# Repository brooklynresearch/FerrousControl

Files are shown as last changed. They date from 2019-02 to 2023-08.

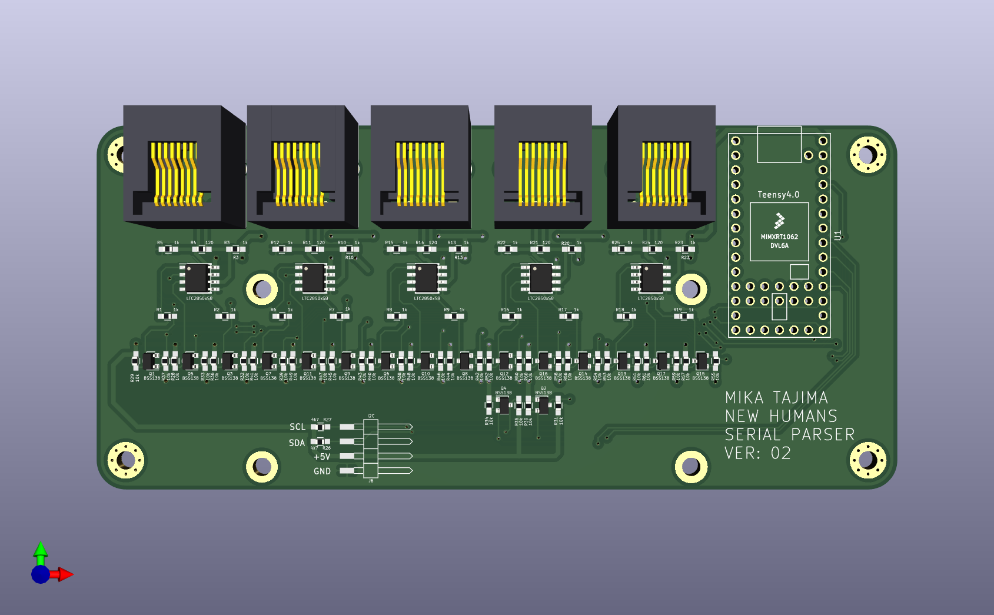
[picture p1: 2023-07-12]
embedded/hardware/SerialParser_V2/SerialParser_V2_Top.png

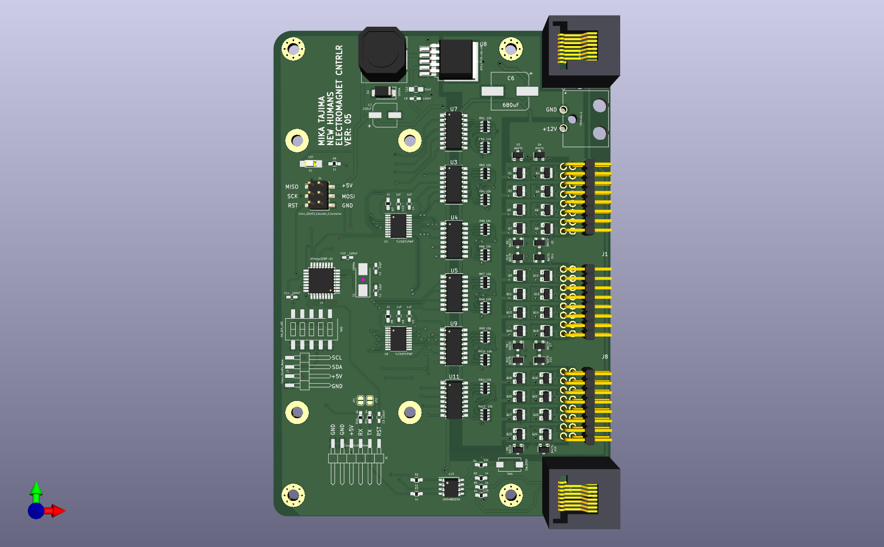
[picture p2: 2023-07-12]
embedded/hardware/ElectromagnetController_V5/ElectromagnetController_V5_top_view.png

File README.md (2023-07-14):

# FerrousControl
Ferrofluid controlled through an electromagnetic array

## python
This folder contains all the algorithms and code to send to the electromagnetic array.

## embedded
This folder contains all the design files and embedded code for the electromagentic controller boards.
These basically received USB Serial messages from the main computer, parse that information to the proper board, and translate those messages to the electromagnets.

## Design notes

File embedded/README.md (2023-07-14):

# Embedded

## hardware
This folder contains the schematics and board layout files for the electromagnetic controller and the serial parser boards.

## production
This folder contains all the production files for the electromagnetic controller and serial parser boards.

## software
This folder contatins all the arduino code and libraries used for both the electromagnetic controller and serial parser boards.

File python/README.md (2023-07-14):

# FerrousControl
Ferrofluid controlled through an electromagnetic array

## COMMS
Requirements:
- Python 3.6.2
- PySerial
- [Robust Serial Library](https://github.com/araffin/arduino-robust-serial)

## PYTHON
- steps variable in snake effectively changes speed with fewer steps being faster
- framerate also adjusts speed but for everything at once
- keyboard toggle for modes needs rewrite
- original code may have an issue with viscosity in fluid class with viscosity

## Startup
- java -jar /Users/newhumans/Documents/GitHub/FerrousControl/COMMS/PYTHON/nstokes_2_40x46/processing-py.jar /Users/newhumans/Documents/GitHub/FerrousControl/COMMS/PYTHON/nstokes_2_40x46/nstokes_2_40x46.pyde
- above was done as part of a Utilities Automator script that starts on login

### Resources
- [USB Serial Communication](https://www.pjrc.com/teensy/td_serial.html)
- [Serial Benchmark](https://www.pjrc.com/teensy/benchmark_usb_serial_receive.html)
- [TLC59711 Datasheet] (https://www.ti.com/lit/ds/symlink/tlc59711.pdf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)

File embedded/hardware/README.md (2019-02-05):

# FerrousControl
Ferrofluid controlled through an electromagnetic array

## PCB DESIGN
Using Eagle for CAD work.  Go to folder for more information

## RASPBERRY PI CODE
To be uploaded, with any steps for set up and functionality.

## EMBEDDED CODE
TO DO

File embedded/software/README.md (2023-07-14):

# Software
Arduino Based Code for both the Electromagnetic Controller and Serial Parser.

## Notes on the Electromagnetic Control
Code was based on the atmega328 chip set, however due to supply chain issues we used the atmega168 chip set.
Regardless, we needed to modify the hardware serial buffer to support 256 bytes, which was required in order to allow for full throughput of serial data.  The default serial buffer size is set to 64 bytes, and would cause overflow on the data being received on the RS485 line.
Liquid Crystal display is not needed, an only used for testing and feedback purposes.  It can be removed if needed.

## Notes on the Serial Parser
Code was based on the Teensy 4.0 development board.  
Liquid Cyrstal display is not needed, an only used for testing and feedback purposes.  It can be removed if needed.

## Platform
- Tested on Arduino 2.11

## Dependecies:
- [Teensyduino](https://www.pjrc.com/teensy/teensyduino.html)
- [MiniCore] (https://github.com/MCUdude/MiniCore)
- [LiquidCrystal_I2C] (https://github.com/johnrickman/LiquidCrystal_I2C)
- [TLC59711] (https://github.com/s-light/ulrichstern_Tlc59711/tree/master/examples)

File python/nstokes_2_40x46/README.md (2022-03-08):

# nstokes version 2
### 40 x 46 magnets

#### Launch Command
```
java -jar processing-py.jar nstokes_2_40x46.pyde
```

#### Keyboard Controls
* `s` Toggle SNEK mode
* `m` Toggle MORPH mode
* `t` Toggle test sequence (if snek or morph is active, toggle that off before using this)
* `o` All magnets on
* `r` Reset all to 0
* `f` Activate area around mouse pointer
* `d` Activate single magnet under mouse pointer

#### Notes

To change the parser board USB addresses, edit the [serialAddresses array](https://github.com/brooklynresearch/FerrousControl/blob/772c967f043f15182d9b4fa4592e4093779d1fde/COMMS/PYTHON/nstokes_2_40x46/nstokes_2_40x46.pyde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)

To have the program run the test sequence only, set [DEBUG_MODE](https://github.com/brooklynresearch/FerrousControl/blob/772c967f043f15182d9b4fa4592e4093779d1fde/COMMS/PYTHON/nstokes_2_40x46/nstokes_2_40x46.pyde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)

**Possible issue**: I've had to restart the parser boards to get the magnet indexing correct. This seems to happen when connecting a magnet controller (or chain of them) to one of the parser's RJ45 ports **after** running the processing sketch.
Sometimes, subsequent runs will have incorrect indexing for the packet that gets sent to the magnet boards. For example, the boards in the lower half will be one row off until a parser restart.
Replugging the USB hub to the computer fixes it. **Needs more testing**

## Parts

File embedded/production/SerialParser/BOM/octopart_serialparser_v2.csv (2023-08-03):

Query | Qty | Manufacturer | MPN | Octopart URL | Part Description | Description | Schematic Reference | Internal Part Number | Lifecycle | Lead Time | RoHS | Total Qty (@ Batch Size: 1) | SKU | SKU | SKU | SKU | SKU | Packaging | Packaging | Packaging | Packaging | Packaging | Unit Price (@ Batch Size: 1) | Unit Price (@ Batch Size: 1) | Unit Price (@ Batch Size: 1) | Unit Price (@ Batch Size: 1) | Unit Price (@ Batch Size: 1) | In Stock | In Stock | In Stock | In Stock | In Stock | MOQ | MOQ | MOQ | MOQ | MOQ | URL | URL | URL | URL | URL | Distributor [Lowest Price (Selected)] | SKU [Lowest Price (Selected)] | Packaging [Lowest Price (Selected)] | Unit Price (@ Batch Size: 1) [Lowest Price (Selected)] | Line Total [Lowest Price (Selected)] | Batch Total [Lowest Price (Selected)] | In Stock [Lowest Price (Selected)] | MOQ [Lowest Price (Selected)] | URL [Lowest Price (Selected)] | Notes
 |  |  |  |  |  |  |  |  |  |  |  |  | Digi-Key | Mouser | Newark | Onlinecomponents.com | RS Components | Digi-Key | Mouser | Newark | Onlinecomponents.com | RS Components | Digi-Key | Mouser | Newark | Onlinecomponents.com | RS Components | Digi-Key | Mouser | Newark | Onlinecomponents.com | RS Components | Digi-Key | Mouser | Newark | Onlinecomponents.com | RS Components | Digi-Key | Mouser | Newark | Onlinecomponents.com | RS Components
RNCP0603FTD10K0 | 34 | Stackpole Electronics | RNCP0603FTD10K0 | https://octopart.com/rncp0603ftd10k0-stackpole+electronics-19220255 | Res Thin Film 0603 10K Ohm 1% 1/8W ±100ppm/°C Molded SMD SMD Paper T/R |  | R28, R29, R30, R31, R32, R33, R34, R35, R36, R37, R38, R39, R40, R41, R42, R43, R44, R45, R46, R47, R48, R49, R50, R51, R52, R53, R54, R55, R56, R57, R58, R59, R60, R61 |  |  | 14w | Compliant | 34 | RNCP0603FTD10K0CT-ND | 708-RNCP0603FTD10K0 |  | RNCP0603FTD10K0 |  | Cut Tape | Tape & Reel |  | Bulk |  | 0.059 | 0.058 |  |  |  | 1127433 | 47188 |  | 55000 |  | 1 | 1 |  | 5000 |  | https://octopart.com/opatz8j6/a1 | https://octopart.com/opatz8j6/a1 |  | https://octopart.com/opatz8j6/a1 |  | Mouser | 708-RNCP0603FTD10K0 | Tape & Reel | 0.058 | 1.9720000000000002 | 1.9720000000000002 | 47188 | 1 | https://octopart.com/opatz8j6/a1
RNCP0603FTD1K00 | 20 | Stackpole Electronics | RNCP0603FTD1K00 | https://octopart.com/rncp0603ftd1k00-stackpole+electronics-19220270 | Res Thin Film 0603 1K Ohm 1% 0.125W(1/8W) ±100ppm/C Sulfur Resistant Pad SMD T/R |  | R1, R2, R3, R5, R6, R7, R8, R9, R10, R12, R13, R15, R16, R17, R18, R19, R20, R22, R23, R25 |  |  | 14w | Compliant | 20 | RNCP0603FTD1K00CT-ND | 708-RNCP0603FTD1K00 |  | RNCP0603FTD1K00 |  | Cut Tape | Tape & Reel |  | Bulk |  | 0.059 | 0.058 |  |  |  | 280655 | 208332 |  | 20000 |  | 1 | 1 |  | 5000 |  | https://octopart.com/opatz8j6/a1 | https://octopart.com/opatz8j6/a1 |  | https://octopart.com/opatz8j6/a1 |  | Mouser | 708-RNCP0603FTD1K00 | Tape & Reel | 0.058 | 1.1600000000000001 | 1.1600000000000001 | 208332 | 1 | https://octopart.com/opatz8j6/a1
RC0603JR-07120RL | 5 | Yageo | RC0603JR-07120RL | https://octopart.com/rc0603jr-07120rl-yageo-40952985 | SMD Chip Resistor, 120 Ohm, ± 5%, 100 mW, 0603 [1608 Metric], Thick Film, General Purpose |  | R4, R11, R14, R21, R24 |  |  | 20w | Compliant | 5 | 311-120GRCT-ND | 603-RC0603JR-07120RL | 68R0151 |  |  | Cut Tape | Tape & Reel |  |  |  | 0.1 | 0.1 | 0.065 |  |  | 445619 | 273445 | 903 |  |  | 1 | 1 | 1 |  |  | https://octopart.com/opatz8j6/a1 | https://octopart.com/opatz8j6/a1 | https://octopart.com/opatz8j6/a1 |  |  | Newark | 68R0151 |  | 0.065 | 0.325 | 0.325 | 903 | 1 | https://octopart.com/opatz8j6/a1
RC0603FR-074K7L | 2 | Yageo | RC0603FR-074K7L | https://octopart.com/rc0603fr-074k7l-yageo-55402884 | SMD Chip Resistor, 4.7 kOhm, ± 1%, 100 mW, 0603 [1608 Metric], Thick Film, General Purpose |  | R26, R27 |  |  | 20w | Compliant | 2 | 311-4.70KHRCT-ND | 603-RC0603FR-074K7L | 75X0151 |  |  | Cut Tape | Tape & Reel |  |  |  | 0.1 | 0.1 |  |  |  | 8525349 | 3530712 | 495000 |  |  | 1 | 1 | 5000 |  |  | https://octopart.com/opatz8j6/a1 | https://octopart.com/opatz8j6/a1 | https://octopart.com/opatz8j6/a1 |  |  | DigiKey | 311-4.70KHRCT-ND | Cut Tape | 0.1 | 0.2 | 0.2 | 8525349 | 1 | https://octopart.com/opatz8j6/a1
SP485ECN-L/TR | 5 | MaxLinear | SP485ECN-L/TR | https://octopart.com/sp485ecn-l%2Ftr-maxlinear-94414514 | SP485E Series 10 Mbps 5 V Enhanced Low EMI Half Duplex RS-485 Transceiver-NSOIC8 |  | U2, U3, U4, U5, U6 |  |  | 8w | Non-Compliant | 5 | 1016-1826-1-ND | 701-SP485ECN-L/TR |  |  |  | Cut Tape | Tape & Reel |  |  |  | 1.02 | 1.02 |  |  |  | 27194 | 48878 |  |  |  | 1 | 1 |  |  |  | https://octopart.com/opatz8j6/a1 | https://octopart.com/opatz8j6/a1 |  |  |  | DigiKey | 1016-1826-1-ND | Cut Tape | 1.02 | 5.1 | 5.1 | 27194 | 1 | https://octopart.com/opatz8j6/a1
DEV-15583 | 1 | SparkFun | DEV-15583 | https://octopart.com/dev-15583-sparkfun-103942182 | iMXRT1062 Microcontroller Development Board 600MHz CPU 1GB RAM 2GB Flash Linux |  | U1 |  |  | 6w |  | 1 | 1568-DEV-15583-ND | 474-DEV-15583 |  | DEV-15583 |  | Bulk |  |  | Bulk |  | 24.99 | 29.98 |  | 29.4 |  | 1164 | 752 |  | 114 |  | 1 | 1 |  | 1 |  | https://octopart.com/opatz8j6/a1 | https://octopart.com/opatz8j6/a1 |  | https://octopart.com/opatz8j6/a1 |  | DigiKey | 1568-DEV-15583-ND | Bulk | 24.99 | 24.99 | 24.99 | 1164 | 1 | https://octopart.com/opatz8j6/a1
BSS138K-13 | 17 | Diodes Inc. | BSS138K-13 | https://octopart.com/bss138k-13-diodes+inc.-91620601 | BSS138 N-Channel 50 V 310 mA 380 mW Surface Mount Mosfet - SOT-23-3 |  | Q1, Q2, Q3, Q4, Q5, Q6, Q7, Q8, Q9, Q10, Q11, Q12, Q13, Q14, Q15, Q16, Q17 |  |  | 8w | Non-Compliant | 17 | BSS138K-13DICT-ND | 621-BSS138K-13 | 28AK6535 |  |  | Cut Tape | Tape & Reel |  |  |  | 0.254 | 0.254 | 0.259 |  |  | 215811 | 389301 | 0 |  |  | 1 | 1 | 5 |  |  | https://octopart.com/opatz8j6/a1 | https://octopart.com/opatz8j6/a1 | https://octopart.com/opatz8j6/a1 |  |  | DigiKey | BSS138K-13DICT-ND | Cut Tape | 0.254 | 4.318 | 4.318 | 215811 | 1 | https://octopart.com/opatz8j6/a1
E5J88-00LJG2-L | 5 | Pulse | E5J88-00LJG2-L | https://octopart.com/e5j88-00ljg2-l-pulse-17223372 | Conn Modular Jack F 8 POS 1.02mm Solder RA Thru-Hole 8 Terminal 1 Port |  | J1, J2, J3, J4, J5 |  | Production (Last Updated: 2 years ago) | 10w | Compliant | 5 | 553-2264-ND | 673-E5J88-00LJG2-L | 54AK6211 | E5J88-00LJG2-L |  | Tray | Bulk |  | Bulk |  | 1.14 | 1.14 |  |  |  | 28658 | 3549 | 0 | 3403 |  | 1 | 1 | 3000 | 30 |  | https://octopart.com/opatz8j6/a1 | https://octopart.com/opatz8j6/a1 | https://octopart.com/opatz8j6/a1 | https://octopart.com/opatz8j6/a1 |  | DigiKey | 553-2264-ND | Tray | 1.14 | 5.699999999999999 | 5.699999999999999 | 28658 | 1 | https://octopart.com/opatz8j6/a1
M20-8890445 | 1 | Harwin | M20-8890445 | https://octopart.com/m20-8890445-harwin-76912496 | Connector, R/a Header, 4POS, 1ROW, 2.54MM; |  | J6 |  |  | 18w | Non-Compliant | 1 | 952-3233-ND | 855-M20-8890445 | 45AJ6361 |  |  | Tube | Tube |  |  |  | 0.66 | 0.66 |  |  |  | 2561 | 51 | 674 |  |  | 1 | 1 | 10 |  |  | https://octopart.com/opatz8j6/a1 | https://octopart.com/opatz8j6/a1 | https://octopart.com/opatz8j6/a1 |  |  | DigiKey | 952-3233-ND | Tube | 0.66 | 0.66 | 0.66 | 2561 | 1 | https://octopart.com/opatz8j6/a1

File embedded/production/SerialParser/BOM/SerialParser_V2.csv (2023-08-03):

Id | Designator | Footprint | Quantity | Designation | Supplier and ref
1 | J1,J2,J3,J4,J5 | RJ45_8 | 5 | 8P8C
2 | R1,R2,R3,R5,R6,R7,R8,R9,R10,R12,R13,R15,R16,R17,R18,R19,R20,R22,R23,R25 | R_0603_HandSoldering | 20 | 1k
3 | R4,R11,R14,R21,R24 | R_0603_HandSoldering | 5 | 120
4 | U2,U5,U6,U3,U4 | SOIC-8_3.9x4.9mm_Pitch1.27mm | 5 | LTC2850xS8
5 | J6 | 4Pin_SMD_Angled_Header_2.54mm | 1 | I2C
6 | R26,R27 | R_0603_HandSoldering | 2 | 4k7
7 | R28,R29,R30,R31,R32,R33,R34,R35,R36,R37,R38,R39,R40,R41,R42,R43,R44,R45,R46,R47,R48,R49,R50,R51,R52,R53,R54,R55,R56,R57,R58,R59,R60,R61 | R_0603_HandSoldering | 34 | 10k
8 | U1 | Teensy40 | 1 | Teensy4.0
9 | Q1,Q2,Q3,Q4,Q5,Q6,Q7,Q8,Q9,Q10,Q11,Q12,Q13,Q14,Q15,Q16,Q17 | SOT-23 | 17 | BSS138

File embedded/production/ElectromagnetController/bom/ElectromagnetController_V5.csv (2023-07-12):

Comment | Designator | Footprint | LCSC
22pF | C1,C2 | Capacitors_SMD:C_0603_HandSoldering | C1653
10uF | C12 | Capacitors_SMD:C_0805_HandSoldering | C15850
100nF | C3,C8,C14,C15 | Capacitors_SMD:C_0603_HandSoldering | C14663
1uF | C4,C5,C9,C13 | Capacitors_SMD:C_0603_HandSoldering | C1592
680uF | C6 | EzerLonginus:13x13_CAP_SMD | C249685
220uF | C7 | Capacitors_SMD:CP_Elec_6.3x7.7
LED | D1 | LEDs:LED_1206_HandSoldering | C130717
1N5822 | D2 | EzerLonginus:SS16 | C669017
BAV70 | D3,D4,D5,D6,D7,D8,D9,D10,D11,D12,D13,D14 | TO_SOT_Packages_SMD:SOT-23 | C402233
MountingHole | H1,H2,H3,H4 | Mounting_Holes:MountingHole_3.2mm_M3_Pad_Via
MountingHole | H5,H6,H7,H8 | Mounting_Holes:MountingHole_3.2mm_M3_Pad
Conn_02x08_Odd_Even | J1,J8,J9 | EzerLonginus:16Pin_8x2_Angled_Header_2.54mm
RJ45_Shielded | J2,J6 | Connectors:RJ45_8
794120-1 | J3 | EzerLonginus:794120-1
Conn_02x03_Counter_Clockwise | J4 | Pin_Headers:Pin_Header_Straight_2x03_Pitch2.54mm_SMD | C721864
Conn_01x06_Male | J5 | EzerLonginus:6Pin_SMD_Angled_Header_2.54mm
Conn_01x04_Male | J7 | EzerLonginus:4Pin_SMD_Angled_Header_2.54mm
Jumper_NO_Small | JP1,JP2 | Jumper:SolderJumper-2_P1.3mm_Open_RoundedPad1.0x1.5mm
33uH | L1 | Inductors_SMD:L_12x12mm_h8mm
Q_NMOS_GSD | Q1,Q2,Q3,Q4,Q5,Q6,Q7,Q8,Q9,Q10,Q11,Q12,Q13,Q14,Q15,Q16,Q17,Q18,Q19,Q20,Q21,Q22,Q23,Q24 | EzerLonginus:SOT23 | C15127
10k | R1 | Resistors_SMD:R_0603_HandSoldering | C99198
1k | R2,R3,R4,R6,R7,R8,R9,R10,R11 | Resistors_SMD:R_0603_HandSoldering | C328340
120 | R5 | Resistors_SMD:R_0603_HandSoldering | C114681
10k | RN1,RN2,RN3,RN4,RN5,RN6,RN7,RN8,RN9,RN10,RN11,RN12 | Resistors_SMD:R_Array_Convex_4x0603 | C107374
SW_SPST | SW1 | Buttons_Switches_SMD:SW_SPST_EVQPE1 | C520860
SW_DIP_x05 | SW2 | Buttons_Switches_SMD:SW_DIP_x5_W8.61mm_Slide_LowProfile | C319036
ATmega328P-AU | U1 | Housings_QFP:TQFP-32_7x7mm_Pitch0.8mm | C8728
UM3486EESA | U10 | Housings_SOIC:SOIC-8_3.9x4.9mm_Pitch1.27mm | C7063
TLC5971PWP | U2,U6 | Housings_SSOP:HTSSOP-20-1EP_4.4x6.5mm_Pitch0.65mm_ThermalPad | C181236
APE1707H-50-HF | U8 | TO_SOT_Packages_SMD:TO-263-5_TabPin3 | C77782
TLP290-4 | U3,U4,U5,U7,U9,U11 | Housings_SSOP:SOP-16_4.4x10.4mm_Pitch1.27mm | C115451
16MHz | Y1 | Crystals:Crystal_SMD_0603-2pin_6.0x3.5mm_HandSoldering | C112572

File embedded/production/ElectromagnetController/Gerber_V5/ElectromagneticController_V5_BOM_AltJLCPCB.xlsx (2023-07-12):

Designator | Comment | Footprint | Quantity | LCSC Part Number
U2,U6 | 12-CHANNEL, 16-BIT ES-PWM RGB LED DRIVER WITH 3.3V LINEAR REGULATOR 20-HTSSOP | 20-HTSSOP | 2 | C181236
Q1,Q2,Q3,Q4,Q5,Q6,Q7,Q8,Q9,Q10,Q11,Q12,Q13,Q14,Q15,Q16,Q17,Q18,Q19,Q20,Q21,Q22,Q23,Q24 | TRANS MOSFET N-CH 30V 5.7A 3-PIN SOT-23 | SOT-23 | 24 | C15127
C6 | 680UF 35V 20% (12.5 X 13MM) | 12.5X13MM | 1 | C249685
D2 | RECTIFIER DIODE SCHOTTKY 40V 5A 2-PIN SMA T/R | SMA | 1 | C669017

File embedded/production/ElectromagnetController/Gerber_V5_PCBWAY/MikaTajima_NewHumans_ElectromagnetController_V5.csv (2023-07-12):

Query | Qty | Manufacturer | MPN | Octopart URL | Part Description | Description | Schematic Reference | Internal Part Number | Lifecycle | Lead Time | RoHS | Total Qty (@ Batch Size: 1) | SKU | SKU | SKU | SKU | SKU | Packaging | Packaging | Packaging | Packaging | Packaging | Unit Price (@ Batch Size: 1) | Unit Price (@ Batch Size: 1) | Unit Price (@ Batch Size: 1) | Unit Price (@ Batch Size: 1) | Unit Price (@ Batch Size: 1) | In Stock | In Stock | In Stock | In Stock | In Stock | MOQ | MOQ | MOQ | MOQ | MOQ | URL | URL | URL | URL | URL | Distributor [Lowest Price (Selected)] | SKU [Lowest Price (Selected)] | Packaging [Lowest Price (Selected)] | Unit Price (@ Batch Size: 1) [Lowest Price (Selected)] | Line Total [Lowest Price (Selected)] | Batch Total [Lowest Price (Selected)] | In Stock [Lowest Price (Selected)] | MOQ [Lowest Price (Selected)] | URL [Lowest Price (Selected)] | Notes
 |  |  |  |  |  |  |  |  |  |  |  |  | Digi-Key | Mouser | Newark | Onlinecomponents.com | RS Components | Digi-Key | Mouser | Newark | Onlinecomponents.com | RS Components | Digi-Key | Mouser | Newark | Onlinecomponents.com | RS Components | Digi-Key | Mouser | Newark | Onlinecomponents.com | RS Components | Digi-Key | Mouser | Newark | Onlinecomponents.com | RS Components | Digi-Key | Mouser | Newark | Onlinecomponents.com | RS Components
CL10C220JB8NFNC | 2 | Samsung | CL10C220JB8NFNC | https://octopart.com/cl10c220jb8nfnc-samsung-24958047 | Cap Ceramic 22pF 50V C0G 5% SMD 0603 125°C Paper T/R |  | C1, C2 |  | Production (Last Updated: 2 years ago) | 28w | Compliant | 2 | 1276-2228-1-ND | 187-CL10C220JB8NFNC |  |  |  | Cut Tape | Tape & Reel |  |  |  | 0.1 | 0.1 |  |  |  | 0 | 111964 |  |  |  | 1 | 1 |  |  |  | https://octopart.com/click/track?ai4=706&country=US&ct=offers&ppid=24958047&sid=459&sig=0905411&vpid=72525017 | https://octopart.com/click/track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 |  |  |  | Digi-Key | 1276-2228-1-ND | Cut Tape | 0.1 | 0.2 | 0.2 | 0 | 1 | https://octopart.com/click/track?ai4=706&country=US&ct=offers&ppid=24958047&sid=459&sig=0905411&vpid=72525017
CL10B104KB8NNNL | 4 | Samsung | CL10B104KB8NNNL | https://octopart.com/cl10b104kb8nnnl-samsung-21395620 | CL10 Series 0603 0.1 uF 50 V ±10% Tolerance X7R Multilayer Ceramic Capacitor |  | C3,C8,C14,C15 |  | Production (Last Updated: 2 years ago) | 28w | Compliant | 4 | 1276-CL10B104KB8NNNLCT-ND | 187-CL10B104KB8NNNL |  |  |  | Cut Tape | Tape & Reel |  |  |  | 0.1 | 0.1 |  |  |  | 2211407 | 258476 |  |  |  | 1 | 1 |  |  |  | https://octopart.com/click/track?ai4=706&country=US&ct=offers&ppid=21395620&sid=459&sig=0e9765d&vpid=578720948 | https://octopart.com/click/track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 |  |  |  | Digi-Key | 1276-CL10B104KB8NNNLCT-ND | Cut Tape | 0.1 | 0.4 | 0.4 | 2211407 | 1 | https://octopart.com/click/track?ai4=706&country=US&ct=offers&ppid=21395620&sid=459&sig=0e9765d&vpid=578720948
CL10A105KA8NNNC | 4 | Samsung | CL10A105KA8NNNC | https://octopart.com/cl10a105ka8nnnc-samsung-9300957 | Ceramic capacitor SMD-0603 1000nF/25V X7R# K +-10%, Samsung, RoHS |  | C4,C5,C9,C13 |  | Production (Last Updated: 2 years ago) | 28w | Compliant | 4 | 1276-1102-1-ND | 187-CL10A105KA8NNNC | 82AC9275 |  | 7664838 | Cut Tape | Tape & Reel |  |  |  | 0.1 | 0.1 | 0.125 |  |  | 0 | 5831 | 28235 |  | 316000 | 1 | 1 | 1 |  | 4000 | https://octopart.com/click/track?ai4=706&country=US&ct=offers&ppid=9300957&sid=459&sig=02e1842&vpid=72523541 | https://octopart.com/click/track?ai4=706&country=US&ct=offers&ppid=9300957&sid=2401&sig=0b70193&vpid=659501016 | https://octopart.com/click/track?ai4=706&country=US&ct=offers&ppid=9300957&sid=2402&sig=0115595&vpid=511545380 |  | https://octopart.com/click/track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 | Digi-Key | 1276-1102-1-ND | Cut Tape | 0.1 | 0.4 | 0.4 | 0 | 1 | https://octopart.com/click/track?ai4=706&country=US&ct=offers&ppid=9300957&sid=459&sig=02e1842&vpid=72523541
MAL215099013E3 | 1 | Vishay | MAL215099013E3 | https://octopart.com/mal215099013e3-vishay-44434450 | Cap Aluminum 680uF 35V 20% (12.5 X 16mm) SMD 1007mA 1000 hr 105°C Blister T/R |  | C6 |  |  | 26w | Compliant | 1 | 4398PHCT-ND | 594-MAL215099013E3 | 14AC4386 |  |  | Cut Tape | Tape & Reel |  |  |  | 3.28 | 3.28 | 3.12 |  |  | 245 | 0 | 0 |  |  | 1 | 1 | 1 |  |  | https://octopart.com/click/track?ai4=706&country=US&ct=offers&ppid=44434450&sid=459&sig=0551222&vpid=34053374 | https://octopart.com/click/track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 | https://octopart.com/click/track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 |  |  | Newark | 14AC4386 |  | 3.12 | 3.12 | 3.12 | 0 | 1 | https://octopart.com/click/track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
EXV227M016A9HAA | 1 | KEMET | EXV227M016A9HAA | https://octopart.com/exv227m016a9haa-kemet-24151949 | Cap Aluminum 220uF 16V 20% (6.3 X 7.7mm) Solder Pin Cylindrical 340 mOhm 196mA 3000hr 105°C T/R |  | C7 |  |  | 48w | Compliant | 1 | 399-EXV227M016A9HAACT-ND | 80-EXV227M016A9HAA | 28W1715 |  |  | Cut Tape | Tape & Reel |  |  |  | 0.73 | 0.73 | 0.62 |  |  | 240 | 0 | 0 |  |  | 1 | 1 | 1 |  |  | https://octopart.com/click/track?ai4=706&country=US&ct=offers&ppid=24151949&sid=459&sig=0fc373c&vpid=709644915 | https://octopart.com/click/track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 | https://octopart.com/click/track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 |  |  | Newark | 28W1715 |  | 0.62 | 0.62 | 0.62 | 0 | 1 | https://octopart.com/click/track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
CL21A106KAYNNNE | 1 | Samsung | CL21A106KAYNNNE | https://octopart.com/cl21a106kaynnne-samsung-19832166 | Cap Ceramic 10uF 25V X5R 10% SMD 0805 85°C Embossed T/R |  | C12 |  | Production (Last Updated: 2 years ago) | 28w | Compliant | 1 | 1276-2891-1-ND | 187-CL21A106KAYNNNE | 82AC9387 |  |  | Cut Tape | Tape & Reel |  |  |  | 0.2 | 0.2 | 0.25 |  |  | 0 | 1523 | 1970 |  |  | 1 | 1 | 1 |  |  | https://octopart.com/click/track?ai4=706&country=US&ct=offers&ppid=19832166&sid=459&sig=0010341&vpid=72525712 | https://octopart.com/click/track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 | https://octopart.com/click/track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 |  |  | Digi-Key | 1276-2891-1-ND | Cut Tape | 0.2 | 0.2 | 0.2 | 0 | 1 | https://octopart.com/click/track?ai4=706&country=US&ct=offers&ppid=19832166&sid=459&sig=0010341&vpid=72525712
150120BS75000 | 1 | Würth Elektronik | 150120BS75000 | https://octopart.com/150120bs75000-w%C3%BCrth+elektronik-29717786 | Led, Blue, 470 Nm, 3.2 V, 30 Ma, 145 Mcd Rohs Compliant: Yes |  | D1 |  |  | 17w | Compliant | 1 | 732-4989-1-ND | 710-150120BS75000 | 95W3806 |  | 8154243 | Cut Tape | Tape & Reel |  |  |  | 0.22 | 0.22 |  |  |  | 1972 | 26703 | 2738 |  | 700 | 1 | 1 | 5 |  | 50 | https://octopart.com/click/track?ai4=706&country=US&ct=offers&ppid=29717786&sid=459&sig=0535c43&vpid=91297482 | https://octopart.com/click/track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 | https://octopart.com/click/track?ai4=706&country=US&ct=offers&ppid=29717786&sid=2402&sig=0ba8803&vpid=82629816 |  | https://octopart.com/click/track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 | Digi-Key | 732-4989-1-ND | Cut Tape | 0.22 | 0.22 | 0.22 | 1972 | 1 | https://octopart.com/click/track?ai4=706&country=US&ct=offers&ppid=29717786&sid=459&sig=0535c43&vpid=91297482
SK54A-LTP | 1 | MCC | SK54A-LTP | https://octopart.com/sk54a-ltp-mcc-53603099 | Rectifier Diode Schottky 40V 5A 2-Pin SMA T/R |  | D2 |  |  | 17w | Compliant | 1 | SK54A-LTPMSCT-ND | 833-SK54A-LTP |  |  |  | Cut Tape | Tape & Reel |  |  |  | 0.51 | 0.5 |  |  |  | 2549 | 12096 |  |  |  | 1 | 1 |  |  |  | https://octopart.com/click/track?ai4=706&country=US&ct=offers&ppid=53603099&sid=459&sig=0bd3552&vpid=180698753 | https://octopart.com/click/track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 |  |  |  | Mouser | 833-SK54A-LTP | Tape & Reel | 0.5 | 0.5 | 0.5 | 12096 | 1 | https://octopart.com/click/track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
BAV70-E3-08 | 12 | Vishay | BAV70-E3-08 | https://octopart.com/bav70-e3-08-vishay-46456617 | Rectifier Diode Small Signal Switching Si 70V 0.25A 6ns 3-Pin SOT-23 T/R |  | D3,D4,D5,D6,D7,D8,D9,D10,D11,D12,D13,D14 |  |  | 52w | Compliant | 12 | BAV70-E3-08CT-ND | 78-BAV70-E3-08 | 09X2414 |  | 8151232 | Cut Tape | Tape & Reel |  |  |  | 0.189 | 0.189 |  |  |  | 16083 | 3413 | 0 |  | 800 | 1 | 1 | 15000 |  | 300 | https://octopart.com/click/track?ai4=706&country=US&ct=offers&ppid=46456617&sid=459&sig=001eafe&vpid=159729154 | https://octopart.com/click/track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 | https://octopart.com/click/track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 |  | https://octopart.com/click/track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 | Digi-Key | BAV70-E3-08CT-ND | Cut Tape | 0.189 | 2.268 | 2.268 | 16083 | 1 | https://octopart.com/click/track?ai4=706&country=US&ct=offers&ppid=46456617&sid=459&sig=001eafe&vpid=159729154
SBH11-PBPC-D08-RA-BK | 3 | Sullins | SBH11-PBPC-D08-RA-BK | https://octopart.com/sbh11-pbpc-d08-ra-bk-sullins-19121459 | 16 Position Total Dual Row 2.54 mm Pitch Right Angle Male Shrouded Box Header |  | J1,J8,J9 |  |  | 11w | Compliant | 3 | S9179-ND |  |  |  |  | Tray |  |  |  |  | 0.73 |  |  |  |  | 3448 |  |  |  |  | 1 |  |  |  |  | https://octopart.com/click/track?ai4=706&country=US&ct=offers&ppid=19121459&sid=459&sig=06e3ac5&vpid=33973875 |  |  |  |  | Digi-Key | S9179-ND | Tray | 0.73 | 2.19 | 2.19 | 3448 | 1 | https://octopart.com/click/track?ai4=706&country=US&ct=offers&ppid=19121459&sid=459&sig=06e3ac5&vpid=33973875
SS-90000-001 | 2 | Stewart Connector | SS-90000-001 | https://octopart.com/ss-90000-001-stewart+connector-119108744 | Right-angle Dual Port D-Sub Connector |  | J2,J6 |  |  | 14w |  | 2 | 380-SS-90000-001-ND |  | 53AJ8404 |  |  | Tray |  |  |  |  | 0.74 |  | 0.259 |  |  | 1901 |  | 2580 |  |  | 1 |  | 1 |  |  | https://octopart.com/click/track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 |  | https://octopart.com/click/track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 |  |  | Newark | 53AJ8404 |  | 0.259 | 0.518 | 0.518 | 2580 | 1 | https://octopart.com/click/track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
794120-1 | 1 | TE Connectivity | 794120-1 | https://octopart.com/794120-1-te+connectivity-39534315 | Conn Power HDR 2 POS 5.08mm Solder RA Thru-Hole 2 Terminal 1 Port Automotive Bag |  | J3 |  | Production (Last Updated: 1 week ago) | 22w | Compliant | 1 | A25753-ND | 571-7941201 | 13M4085 | 794120-1 | 0520349P | Bulk | Bulk |  | Bulk |  | 3.1 | 2.95 | 2.14 |  |  | 3326 | 225 | 0 | 83 | 0 | 1 | 1 | 1 | 100 | 10 | https://octopart.com/click/track?ai4=706&country=US&ct=offers&ppid=39534315&sid=459&sig=072132b&vpid=198762547 | https://octopart.com/click/track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 | https://octopart.com/click/track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 | https://octopart.com/click/track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 | https://octopart.com/click/track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 | Newark | 13M4085 |  | 2.14 | 2.14 | 2.14 | 0 | 1 | https://octopart.com/click/track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
M20-8750342 | 1 | Harwin | M20-8750342 | https://octopart.com/m20-8750342-harwin-76713899 | Connector, Header, 6Pos, 2.54Mm, 2Row Rohs Compliant: Yes |  | J4 |  |  | 14w | Non-Compliant | 1 | 952-3157-ND | 855-M20-8750342 | 29AH6764 |  |  | Tube | Tube |  |  |  | 0.48 | 0.47 |  |  |  | 1719 | 776 | 40 |  |  | 1 | 1 | 10 |  |  | https://octopart.com/click/track?ai4=706&country=US&ct=offers&ppid=76713899&sid=459&sig=0f3c98d&vpid=277482621 | https://octopart.com/click/track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 | https://octopart.com/click/track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 |  |  | Mouser | 855-M20-8750342 | Tube | 0.47 | 0.47 | 0.47 | 776 | 1 | https://octopart.com/click/track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
M20-8890645 | 1 | Harwin | M20-8890645 | https://octopart.com/m20-8890645-harwin-76912500 | Connector, Header, 6Pos, 2.54Mm, 1Row Rohs Compliant: Yes |  | J5 |  |  | 14w | Non-Compliant | 1 | 952-3235-ND | 855-M20-8890645 | 29AH6781 |  |  | Tube | Tube |  |  |  | 0.83 | 0.8 |  |  |  | 3796 | 730 | 140 |  |  | 1 | 1 | 10 |  |  | https://octopart.com/click/track?ai4=706&country=US&ct=offers&ppid=76912500&sid=459&sig=0a1ee7e&vpid=278066743 | https://octopart.com/click/track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 | https://octopart.com/click/track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 |  |  | Mouser | 855-M20-8890645 | Tube | 0.8 | 0.8 | 0.8 | 730 | 1 | https://octopart.com/click/track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
M20-8890445 | 1 | Harwin | M20-8890445 | https://octopart.com/m20-8890445-harwin-76912496 | 4 Pos. Male SIL Horizontal SMT Conn RoHS Compliant: Yes |  | J7 |  |  | 14w | Non-Compliant | 1 | 952-3233-ND | 855-M20-8890445 | 52AC5016 |  |  | Tube | Tube |  |  |  | 0.61 | 0.59 |  |  |  | 4076 | 805 | 0 |  |  | 1 | 1 | 1254 |  |  | https://octopart.com/click/track?ai4=706&country=US&ct=offers&ppid=76912496&sid=459&sig=0e2b802&vpid=278066739 | https://octopart.com/click/track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 | https://octopart.com/click/track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 |  |  | Mouser | 855-M20-8890445 | Tube | 0.59 | 0.59 | 0.59 | 805 | 1 | https://octopart.com/click/track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
744770133 | 1 | Würth Elektronik | 744770133 | https://octopart.com/744770133-w%C3%BCrth+elektronik-22866874 | Power Choke Shielded Wirewound 33uH 20% 1KHz Ferrite 3.2A 64mOhm DCR T/R |  | L1 |  |  | 26w | Compliant | 1 | 732-1229-1-ND | 710-744770133 | 88T7068 |  | 7444876P | Cut Tape | Tape & Reel |  |  |  | 2.33 | 2.33 | 2.33 |  | 2.46 | 146 | 152 | 5681 |  | 0 | 1 | 1 | 1 |  | 1 | https://octopart.com/click/track?ai4=706&country=US&ct=offers&ppid=22866874&sid=459&sig=04386c7&vpid=33976567 | https://octopart.com/click/track?ai4=706&country=US&ct=offers&ppid=22866874&sid=2401&sig=0475171&vpid=37876672 | https://octopart.com/click/track?ai4=706&country=US&ct=offers&ppid=22866874&sid=2402&sig=051d3f9&vpid=49998547 |  | https://octopart.com/click/track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 | Digi-Key | 732-1229-1-ND | Cut Tape | 2.33 | 2.33 | 2.33 | 146 | 1 | https://octopart.com/click/track?ai4=706&country=US&ct=offers&ppid=22866874&sid=459&sig=04386c7&vpid=33976567
AO3400A | 24 | Alpha & Omega Semiconductor | AO3400A | https://octopart.com/ao3400a-alpha+%26+omega+semiconductor-10533924 | Trans MOSFET N-CH 30V 5.7A 3-Pin SOT-23 |  | Q1,Q2,Q3,Q4,Q5,Q6,Q7,Q8,Q9,Q10,Q11,Q12,Q13,Q14,Q15,Q16,Q17,Q18,Q19,Q20,Q21,Q22,Q23,Q24 |  | NRND (Last Updated: 2 years ago) | 42w | Compliant | 24 | 785-1000-1-ND |  |  |  |  | Cut Tape |  |  |  |  | 0.362 |  |  |  |  | 2 |  |  |  |  | 1 |  |  |  |  | https://octopart.com/click/track?ai4=706&country=US&ct=offers&ppid=10533924&sid=459&sig=0f36b1c&vpid=34206144 |  |  |  |  | Digi-Key | 785-1000-1-ND | Cut Tape | 0.362 | 8.687999999999999 | 8.687999999999999 | 2 | 1 | https://octopart.com/click/track?ai4=706&country=US&ct=offers&ppid=10533924&sid=459&sig=0f36b1c&vpid=34206144
CR0603-FX-1002ELF | 1 | Bourns | CR0603-FX-1002ELF | https://octopart.com/cr0603-fx-1002elf-bourns-2326648 | Res Thick Film 0603 10K Ohm 1% 1/10W ±100ppm/°C Molded SMD SMD Paper Tape on Plastic Reel |  | R1 |  |  | 20w | Compliant | 1 | CR0603-FX-1002ELFCT-ND | 652-CR0603FX-1002ELF | 02J1982 | CR0603-FX-1002ELF | 7408805 | Cut Tape | Tape & Reel |  | Bulk |  | 0.1 | 0.1 | 0.1 |  |  | 0 | 1264959 | 1796 | 125282 | 7700 | 1 | 1 | 1 | 5000 | 50 | https://octopart.com/click/track?ai4=706&country=US&ct=offers&ppid=2326648&sid=459&sig=032e4f0&vpid=54325019 | https://octopart.com/click/track?ai4=706&country=US&ct=offers&ppid=2326648&sid=2401&sig=06c0dac&vpid=37711053 | https://octopart.com/click/track?ai4=706&country=US&ct=offers&ppid=2326648&sid=2402&sig=0468cd9&vpid=3177340 | https://octopart.com/click/track?ai4=706&country=US&ct=offers&ppid=2326648&sid=2429&sig=06d0793&vpid=92278495 | https://octopart.com/click/track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 | Digi-Key | CR0603-FX-1002ELFCT-ND | Cut Tape | 0.1 | 0.1 | 0.1 | 0 | 1 | https://octopart.com/click/track?ai4=706&country=US&ct=offers&ppid=2326648&sid=459&sig=032e4f0&vpid=54325019
MCT06030C1001FP500 | 9 | Vishay | MCT06030C1001FP500 | https://octopart.com/mct06030c1001fp500-vishay-46566501 | Res Thin Film 0603 1K Ohm 1% 1/10W ±50ppm/°C Molded SMD SMD Paper T/R |  | R2,R3,R4,R6,R7,R8,R9,R10,R11 |  |  | 52w | Compliant | 9 | MCT0603-1.00K-CFCT-ND | 594-MCT06030C1001FP5 | 65AC3533 |  | 1885949 | Cut Tape | Tape & Reel |  |  |  | 0.15 | 0.15 | 0.163 |  |  | 6165 | 10205 | 8827 |  | 0 | 1 | 1 | 1 |  | 100 | https://octopart.com/click/track?ai4=706&country=US&ct=offers&ppid=46566501&sid=459&sig=0c405b8&vpid=657632717 | https://octopart.com/click/track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 | https://octopart.com/click/track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 |  | https://octopart.com/click/track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 | Digi-Key | MCT0603-1.00K-CFCT-ND | Cut Tape | 0.15 | 1.3499999999999999 | 1.3499999999999999 | 6165 | 1 | https://octopart.com/click/track?ai4=706&country=US&ct=offers&ppid=46566501&sid=459&sig=0c405b8&vpid=657632717
CRGCQ0603F120R | 1 | TE Connectivity | CRGCQ0603F120R | https://octopart.com/crgcq0603f120r-te+connectivity-91018039 | Res Thick Film 0603 120 Ohm 1% 0.1W(1/10W) ±100ppm/C Pad SMD Automotive T/R |  | R5 |  | Production (Last Updated: 1 week ago) | 21w | Non-Compliant | 1 | A129677CT-ND | 279-CRGCQ0603F120R | 73AC9054 | CRGCQ0603F120R |  | Cut Tape | Tape & Reel |  | Bulk |  | 0.1 | 0.16 | 0.004 |  |  | 2224 | 2025 | 7580 | 0 |  | 1 | 1 | 1 | 5000 |  | https://octopart.com/click/track?ai4=706&country=US&ct=offers&ppid=91018039&sid=459&sig=06a2d35&vpid=475508349 | https://octopart.com/click/track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 | https://octopart.com/click/track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 | https://octopart.com/click/track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 |  | Newark | 73AC9054 |  | 0.004 | 0.004 | 0.004 | 7580 | 1 | https://octopart.com/click/track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
CAY16-103J4LF | 12 | Bourns | CAY16-103J4LF | https://octopart.com/cay16-103j4lf-bourns-152968 | Res Thick Film Array 10K Ohm 5% 0.25W(1/4W) ±200ppm/C ISOL 8-Pin 1206(4 X 0603) Convex SMD T/R |  | RN1,RN2,RN3,RN4,RN5,RN6,RN7,RN8,RN9,RN10,RN11,RN12 |  |  | 18w | Compliant | 12 | CAY16-103J4LFCT-ND | 652-CAY16-103J4LF | 41R4421 | CAY16-103J4LF | 5225585 | Cut Tape | Tape & Reel |  | Bulk |  | 0.065 | 0.067 | 0.105 |  |  | 2022 | 1303946 | 35740 | 95000 | 3500 | 1 | 1 | 10 | 5000 | 50 | https://octopart.com/click/track?ai4=706&country=US&ct=offers&ppid=152968&sid=459&sig=02f4f35&vpid=50630140 | https://octopart.com/click/track?ai4=706&country=US&ct=offers&ppid=152968&sid=2401&sig=0cd22f2&vpid=37748884 | https://octopart.com/click/track?ai4=706&country=US&ct=offers&ppid=152968&sid=2402&sig=03c95bb&vpid=462273179 | https://octopart.com/click/track?ai4=706&country=US&ct=offers&ppid=152968&sid=2429&sig=038684b&vpid=92278303 | https://octopart.com/click/track?ai4=706&country=US&ct=offers&ppid=152968&sid=10022&sig=02e8748&vpid=575451862 | Digi-Key | CAY16-103J4LFCT-ND | Cut Tape | 0.065 | 0.78 | 0.78 | 2022 | 1 | https://octopart.com/click/track?ai4=706&country=US&ct=offers&ppid=152968&sid=459&sig=02f4f35&vpid=50630140
EVQ-PE104K | 1 | Panasonic | EVQ-PE104K | https://octopart.com/evq-pe104k-panasonic-39801593 | Switch Tactile ON OFF SPST Rectangular Button J-Bend 0.05A 12VDC 1N SMD Embossed Tape |  | SW1 |  |  | 8w | Compliant | 1 | P13593SCT-ND | 667-EVQ-PE104K | 83T2745 | EVQ-PE104K | 1250220 | Cut Tape | Tape & Reel |  | Bulk |  | 0.61 | 0.55 | 0.596 |  |  | 42 | 4130 | 2966 | 1750 | 0 | 1 | 1 | 1 | 625 | 10 | https://octopart.com/click/track?ai4=706&country=US&ct=offers&ppid=39801593&sid=459&sig=0ea3b54&vpid=114964596 | https://octopart.com/click/track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 | https://octopart.com/click/track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 | https://octopart.com/click/track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 | https://octopart.com/click/track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 | Mouser | 667-EVQ-PE104K | Tape & Reel | 0.55 | 0.55 | 0.55 | 4130 | 1 | https://octopart.com/click/track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
DS04-254-2-05BK-SMT | 1 | CUI Devices | DS04-254-2-05BK-SMT | https://octopart.com/ds04-254-2-05bk-smt-cui+devices-106794064 | 1 ~ 12 Positions, Surface Mount, 2.54 mm Pitch, Slide Actuator, DIP Switch |  | SW2 |  | Production (Last Updated: 2 years ago) | 8w |  | 1 | 2223-DS04-254-2-05BK-SMT-ND | 490-DS04254205BK-SMT |  | DS04-254-2-05BK-SMT |  | Tube |  |  | Bulk |  | 0.77 | 0.76 |  |  |  | 894 | 32 |  | 0 |  | 1 | 1 |  | 33 |  | https://octopart.com/click/track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 | https://octopart.com/click/track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 |  | https://octopart.com/click/track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 |  | Mouser | 490-DS04254205BK-SMT |  | 0.76 | 0.76 | 0.76 | 32 | 1 | https://octopart.com/click/track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
ATMEGA168PV-10AN | 1 | Microchip | ATMEGA168PV-10AN | https://octopart.com/atmega168pv-10an-microchip-77759996 | ATMEGA168PV-10AN - IC, 8 Bit Mcu, AVR Mega, 10MHZ, 32-TQFP |  | U1 |  | Production (Last Updated: 1 year ago) | 52w | Compliant | 1 | ATMEGA168PV-10AN-ND | 556-ATMEGA168PV-10AN | 68T2729 | ATMEGA168PV-10AN |  | Tray | Tray |  | Bulk |  |  | 3.92 |  |  |  | 0 | 0 | 0 | 0 |  | 250 | 1 | 250 | 63 |  | https://octopart.com/click/track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 | https://octopart.com/click/track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 | https://octopart.com/click/track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 | https://octopart.com/click/track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 |  | Mouser | 556-ATMEGA168PV-10AN | Tray | 3.92 | 3.92 | 3.92 | 0 | 1 | https://octopart.com/click/track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
TLC5971PWP | 2 | Texas Instruments | TLC5971PWP | https://octopart.com/tlc5971pwp-texas+instruments-20025591 | 12-channel, 16-bit ES-PWM RGB LED driver with 3.3V Linear Regulator 20-HTSSOP -40 to 85 |  | U2,U6 |  | Production (Last Updated: 2 weeks ago) |  | Compliant | 2 | TLC5971PWP-ND | 595-TLC5971PWP |  |  |  | Bulk | Tube |  |  |  |  | 3.92 |  |  |  | 0 | 210 |  |  |  | 210 | 1 |  |  |  | https://octopart.com/click/track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 | https://octopart.com/click/track?ai4=706&country=US&ct=offers&ppid=20025591&sid=2401&sig=04bbfa2&vpid=55010175 |  |  |  | Mouser | 595-TLC5971PWP | Tube | 3.92 | 7.84 | 7.84 | 210 | 1 | https://octopart.com/click/track?ai4=706&country=US&ct=offers&ppid=20025591&sid=2401&sig=04bbfa2&vpid=55010175
TLP290-4 | 6 | Toshiba | TLP290-4(GB-TP,E) | https://octopart.com/tlp290-4%28gb-tp%2Ce%29-toshiba-20281703 | Optocoupler AC-IN 4-CH Transistor DC-OUT 16-Pin SOIC T/R |  | U3,U4,U5,U7,U9,U11 |  |  | 52w | Compliant | 6 | TLP290-4(GB-TPE)DKR-ND | 757-TLP2904GBTPE |  |  |  | Custom Reel | Tape & Reel |  |  |  | 1.26 | 1.24 |  |  |  | 0 | 0 |  |  |  | 1 | 1 |  |  |  | https://octopart.com/click/track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 | https://octopart.com/click/track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 |  |  |  | Mouser | 757-TLP2904GBTPE | Tape & Reel | 1.24 | 7.4399999999999995 | 7.4399999999999995 | 0 | 1 | https://octopart.com/click/track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
TS2596CM550 RNG | 1 | Taiwan Semiconductor | TS2596CM550 RNG | https://octopart.com/ts2596cm550+rng-taiwan+semiconductor-58281874 | Conv DC-DC 4.5V to 40V Step Down Single-Out 5V 3A 6-Pin(5+Tab) D2PAK T/R |  | U8 |  | Production (Last Updated: 2 years ago) | 20w | Compliant | 1 | TS2596CM550RNGCT-ND | 821-TS2596CM550RNG |  |  |  | Cut Tape | Tape & Reel |  |  |  | 3.11 | 3.1 |  |  |  | 116 | 0 |  |  |  | 1 | 1 |  |  |  | https://octopart.com/click/track?ai4=706&country=US&ct=offers&ppid=58281874&sid=459&sig=062fc11&vpid=462998762 | https://octopart.com/click/track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 |  |  |  | Mouser | 821-TS2596CM550RNG | Tape & Reel | 3.1 | 3.1 | 3.1 | 0 | 1 | https://octopart.com/click/track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
SN75ALS176AD | 1 | Texas Instruments | SN75ALS176AD | https://octopart.com/sn75als176ad-texas+instruments-503822 | Differential Bus Transceiver 8-SOIC 0 to 70 |  | U10 |  | Production (Last Updated: 2 weeks ago) | 6w | Compliant | 1 | 296-9955-5-ND | 595-SN75ALS176AD |  |  |  | Tube | Tube |  |  |  | 2.81 | 2.81 |  |  |  | 415 | 283 |  |  |  | 1 | 1 |  |  |  | https://octopart.com/click/track?ai4=706&country=US&ct=offers&ppid=503822&sid=459&sig=0f6b828&vpid=1043688 | https://octopart.com/click/track?ai4=706&country=US&ct=offers&ppid=503822&sid=2401&sig=0fe7ec8&vpid=37824732 |  |  |  | Digi-Key | 296-9955-5-ND | Tube | 2.81 | 2.81 | 2.81 | 415 | 1 | https://octopart.com/click/track?ai4=706&country=US&ct=offers&ppid=503822&sid=459&sig=0f6b828&vpid=1043688
ECS-160-12-30-AEM-TR | 1 | ECS International | ECS-160-12-30-AEM-TR | https://octopart.com/ecs-160-12-30-aem-tr-ecs+international-117130323 | Crystal 16MHz 12pF 2-Pin Surface Mount T/R |  | Y1 |  |  | 25w |  | 1 | 50-ECS-160-12-30-AEM-TRCT-ND | 520-160-12-30-AEM-TR |  |  |  | Cut Tape | Tape & Reel |  |  |  | 0.83 | 0.83 |  |  |  | 490 | 2979 |  |  |  | 1 | 1 |  |  |  | https://octopart.com/click/track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 | https://octopart.com/click/track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 |  |  |  | Digi-Key | 50-ECS-160-12-30-AEM-TRCT-ND | Cut Tape | 0.83 | 0.83 | 0.83 | 490 | 1 | https://octopart.com/click/track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

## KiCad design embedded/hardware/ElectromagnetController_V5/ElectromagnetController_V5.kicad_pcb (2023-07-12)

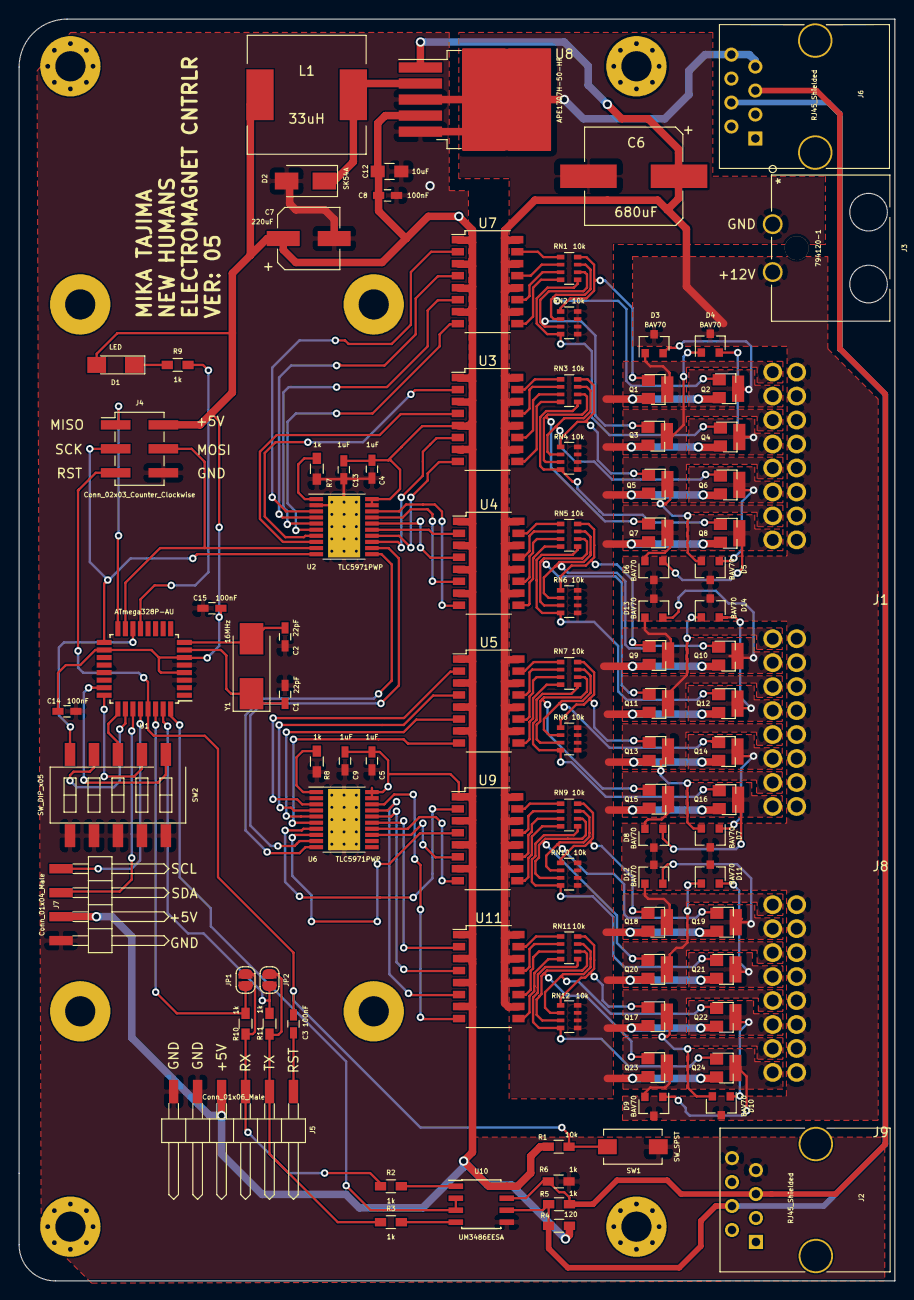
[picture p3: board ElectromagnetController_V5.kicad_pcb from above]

Board: 2 copper layers, 92.8 x 133.8 mm, 108 parts (0 on the bottom side), 129 nets.

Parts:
C1, C2: 22pF; C_0603_HandSoldering
C3, C8, C14, C15: 100nF; C_0603_HandSoldering
C4, C5, C9, C13: 1uF; C_0603_HandSoldering
C6: 680uF; CP_Elec_10x10.5
C7: 220uF; CP_Elec_6.3x7.7
C12: 10uF; C_0805_HandSoldering
D1: LED; LED_1206_HandSoldering
D2: SK54A; D_SMA
D3, D4, D5, D6, D7, D8, D9, D10, D11, D12, D13, D14: BAV70; SOT-23
H1, H2, H3, H4: MountingHole; MountingHole_3.2mm_M3_Pad_Via
H5, H6, H7, H8: MountingHole; MountingHole_3.2mm_M3_Pad
J1, J8, J9: Conn_02x08_Odd_Even; 16Pin_8x2_Angled_Header_2.54mm
J2, J6: RJ45_Shielded; RJ45_8
J3: 794120-1
J4: Conn_02x03_Counter_Clockwise; Pin_Header_Straight_2x03_Pitch2.54mm_SMD
J5: Conn_01x06_Male; 6Pin_SMD_Angled_Header_2.54mm
J7: Conn_01x04_Male; 4Pin_SMD_Angled_Header_2.54mm
JP1, JP2: Jumper_NO_Small; SolderJumper-2_P1.3mm_Open_RoundedPad1.0x1.5mm
L1: 33uH; L_12x12mm_h8mm
Q1, Q2, Q3, Q4, Q5, Q6, Q7, Q8, Q9, Q10, Q11, Q12, Q13, Q14, Q15, Q16, Q17, Q18, Q19, Q20, Q21, Q22, Q23, Q24: Q_NMOS_GSD; SOT-23
R1: 10k; R_0603_HandSoldering
R2, R3, R4, R6, R7, R8, R9, R10, R11: 1k; R_0603_HandSoldering
R5: 120; R_0603_HandSoldering
RN1, RN2, RN3, RN4, RN5, RN6, RN7, RN8, RN9, RN10, RN11, RN12: 10k; R_Array_Convex_4x0603
SW1: SW_SPST; SW_SPST_EVQPE1
SW2: SW_DIP_x05; SW_DIP_x5_W8.61mm_Slide_LowProfile
U1: ATmega328P-AU; TQFP-32_7x7mm_Pitch0.8mm
U2, U6: TLC5971PWP; HTSSOP-20-1EP_4.4x6.5mm_Pitch0.65mm_ThermalPad
U3, U4, U5, U7, U9, U11: TLP290-4; SOP-16_4.4x10.4mm_Pitch1.27mm
U8: APE1707H-50-HF; TO-263-5_TabPin3
U10: UM3486EESA; SOIC-8_3.9x4.9mm_Pitch1.27mm
Y1: 16MHz; Crystal_SMD_0603-2pin_6.0x3.5mm_HandSoldering

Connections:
+5V: C4.1, C5.1, C7.1, C8.1, C9.1, C12.2, C13.1, C14.1, C15.1, D1.2, J4.2, J5.4, J7.3, L1.2, R1.1, R4.1, U1.4, U1.6, U1.18, U2.19, U2.20, U3.1, U3.3, U3.5, U3.7, U4.1, U4.3, U4.5, U4.7, U5.1, U5.3, U5.5, U5.7, U6.19, U6.20, U7.1, U7.3, U7.5, U7.7, U8.4, U9.1, U9.3, U9.5, U9.7, U10.8, U11.1, U11.3, U11.5, U11.7
+12V: C6.1, D3.3, D4.3, D5.3, D6.3, D7.3, D8.3, D9.3, D10.3, D11.3, D12.3, D13.3, D14.3, J1.2, J1.4, J1.6, J1.8, J1.10, J1.12, J1.14, J1.16, J3.2, J8.2, J8.4, J8.6, J8.8, J8.10, J8.12, J8.14, J8.16, J9.2, J9.4, J9.6, J9.8, J9.10, J9.12, J9.14, J9.16, U3.10, U3.12, U3.14, U3.16, U4.10, U4.12, U4.14, U4.16, U5.10, U5.12, U5.14, U5.16, U7.10, U7.12, U7.14, U7.16, U8.1, U9.10, U9.12, U9.14, U9.16, U11.10, U11.12, U11.14, U11.16
/Sheet614B2B13/EM_00: D3.1, J1.1, Q1.3
/Sheet614B2B13/EM_01: D3.2, J1.3, Q2.3
/Sheet614B2B13/EM_02: D4.1, J1.5, Q3.3
/Sheet614B2B13/EM_03: D4.2, J1.7, Q4.3
/Sheet614B2B13/EM_04: D5.2, J1.9, Q5.3
/Sheet614B2B13/EM_05: D5.1, J1.11, Q6.3
/Sheet614B2B13/EM_06: D6.2, J1.13, Q7.3
/Sheet614B2B13/EM_07: D6.1, J1.15, Q8.3
/Sheet614B2B13/EM_08: D13.1, J8.1, Q9.3
/Sheet614B2B13/EM_09: D13.2, J8.3, Q10.3
/Sheet614B2B13/EM_10: D14.1, J8.5, Q11.3
/Sheet614B2B13/EM_11: D14.2, J8.7, Q12.3
/sheet61B8751A/CLK_IN: U2.11, U6.10
/sheet61B8751A/DAT_IN: U2.12, U6.9
/sheet61B8751A/EM_12: D7.2, J8.9, Q13.3
/sheet61B8751A/EM_13: D7.1, J8.11, Q14.3
/sheet61B8751A/EM_14: D8.2, J8.13, Q15.3
/sheet61B8751A/EM_15: D8.1, J8.15, Q16.3
/sheet61B8751A/EM_16: D12.1, J9.1, Q18.3
/sheet61B8751A/EM_17: D12.2, J9.3, Q19.3
/sheet61B8751A/EM_18: D11.1, J9.5, Q20.3
/sheet61B8751A/EM_19: D11.2, J9.7, Q21.3
/sheet61B8751A/EM_20: D10.2, J9.9, Q17.3
/sheet61B8751A/EM_21: D10.1, J9.11, Q22.3
/sheet61B8751A/EM_22: D9.2, J9.13, Q23.3
/sheet61B8751A/EM_23: D9.1, J9.15, Q24.3
A: J2.4, J6.4, R4.2, R5.1, U10.6
B: J2.5, J6.5, R5.2, R6.1, U10.7
DIP0: SW2.1, U1.23
DIP1: SW2.2, U1.24
DIP2: SW2.3, U1.25
DIP3: SW2.4, U1.26
DIP4: SW2.5, U1.14
GND: C1.1, C2.1, C4.2, C5.2, C6.2, C7.2, C8.2, C9.2, C12.1, C13.2, C14.2, C15.2, D2.2, J2.7, J2.8, J3.1, J4.6, J5.5, J5.6, J6.7, J6.8, J7.4, Q1.2, Q2.2, Q3.2, Q4.2, Q5.2, Q6.2, Q7.2, Q8.2, Q9.2, Q10.2, Q11.2, Q12.2, Q13.2, Q14.2, Q15.2, Q16.2, Q17.2, Q18.2, Q19.2, Q20.2, Q21.2, Q22.2, Q23.2, Q24.2, R6.2, R7.2, R8.2, RN2.5, RN2.6, RN2.7, RN2.8, RN4.5, RN4.6, RN4.7, RN4.8, RN6.5, RN6.6, RN6.7, RN6.8, RN8.5, RN8.6, RN8.7, RN8.8, RN10.5, RN10.6, RN10.7, RN10.8, RN12.5, RN12.6, RN12.7, RN12.8, SW1.2, SW2.6, SW2.7, SW2.8, SW2.9, SW2.10, U1.3, U1.5, U1.21, U2.2, U2.21, U6.2, U6.21, U8.3, U8.5, U10.5
MISO: J4.1, U1.16
MOSI: J4.4, U1.15, U2.9
unnamed: C1.2, U1.7, Y1.1
unnamed: C2.2, U1.8, Y1.2
unnamed: C3.1, J5.1
unnamed: D1.1, R9.1
unnamed: D2.1, L1.1, U8.2
unnamed: JP1.1, R10.2, U1.30
unnamed: JP2.1, R11.2, U1.31
unnamed: Q1.1, RN1.8, RN2.1
unnamed: Q2.1, RN1.7, RN2.2
unnamed: Q3.1, RN1.6, RN2.3
unnamed: Q4.1, RN1.5, RN2.4
unnamed: Q5.1, RN3.8, RN4.1
unnamed: Q6.1, RN3.7, RN4.2
unnamed: Q7.1, RN3.6, RN4.3
unnamed: Q8.1, RN3.5, RN4.4
unnamed: Q9.1, RN5.8, RN6.1
unnamed: Q10.1, RN5.7, RN6.2
unnamed: Q11.1, RN5.6, RN6.3
unnamed: Q12.1, RN5.5, RN6.4
unnamed: Q13.1, RN7.8, RN8.1
unnamed: Q14.1, RN7.7, RN8.2
unnamed: Q15.1, RN7.6, RN8.3
unnamed: Q16.1, RN7.5, RN8.4
unnamed: Q17.1, RN11.8, RN12.1
unnamed: Q18.1, RN9.8, RN10.1
unnamed: Q19.1, RN9.7, RN10.2
unnamed: Q20.1, RN9.6, RN10.3
unnamed: Q21.1, RN9.5, RN10.4
unnamed: Q22.1, RN11.7, RN12.2
unnamed: Q23.1, RN11.6, RN12.3
unnamed: Q24.1, RN11.5, RN12.4
unnamed: R2.2, U10.1
unnamed: R3.2, U10.4
unnamed: R7.1, U2.1
unnamed: R8.1, U6.1
unnamed: R9.2, U1.13
unnamed: RN1.1, U7.15
unnamed: RN1.2, U7.13
unnamed: RN1.3, U7.11
unnamed: RN1.4, U7.9
unnamed: RN3.1, U3.15
unnamed: RN3.2, U3.13
unnamed: RN3.3, U3.11
unnamed: RN3.4, U3.9
unnamed: RN5.1, U4.15
unnamed: RN5.2, U4.13
unnamed: RN5.3, U4.11
unnamed: RN5.4, U4.9
unnamed: RN7.1, U5.15
unnamed: RN7.2, U5.13
unnamed: RN7.3, U5.11
unnamed: RN7.4, U5.9
unnamed: RN9.1, U9.15
unnamed: RN9.2, U9.13
unnamed: RN9.3, U9.11
unnamed: RN9.4, U9.9
unnamed: RN11.1, U11.15
unnamed: RN11.2, U11.13
unnamed: RN11.3, U11.11
unnamed: RN11.4, U11.9
PWM_00: U2.3, U7.2
PWM_01: U2.4, U7.4
PWM_02: U2.5, U7.6
PWM_03: U2.6, U7.8
PWM_04: U2.7, U3.2
PWM_05: U2.8, U3.4
PWM_06: U2.13, U3.6
PWM_07: U2.14, U3.8
PWM_08: U2.15, U4.2
PWM_09: U2.16, U4.4
PWM_10: U2.17, U4.6
PWM_11: U2.18, U4.8
PWM_12: U5.2, U6.3
PWM_13: U5.4, U6.4
PWM_14: U5.6, U6.5
PWM_15: U5.8, U6.6
PWM_16: U6.7, U9.2
PWM_17: U6.8, U9.4
PWM_18: U6.13, U9.6
PWM_19: U6.14, U9.8
PWM_20: U6.15, U11.2
PWM_21: U6.16, U11.4
PWM_22: U6.17, U11.6
PWM_23: U6.18, U11.8
RS485: U1.32, U10.2, U10.3
RST: C3.2, J4.5, R1.2, SW1.1, U1.29
RX: J5.3, JP1.2, R2.1, R10.1
SCK: J4.3, U1.17, U2.10
SCL: J7.1, U1.28
SDA: J7.2, U1.27
TX: J5.2, JP2.2, R3.1, R11.1

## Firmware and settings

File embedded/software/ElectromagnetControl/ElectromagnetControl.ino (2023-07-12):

// include the library code:
#include <Wire.h>
#include <LiquidCrystal_I2C.h>
#include <Tlc59711.h>


#define VERSION 1.0
#define DATA_DIR_PIN  2
#define NUM_TLC 2

LiquidCrystal_I2C lcd(0x27, 16, 2);

uint8_t COL = 1;

//#define TESTER
//#define BOARD_TEST
//#define COMMS_TEST

#define ADDR_PIN_1   A0
#define ADDR_PIN_2   A1
#define ADDR_PIN_4   A2
#define ADDR_PIN_8   A3
#define ADDR_PIN_16  10
uint8_t ADDRESS_PIN[5] = {ADDR_PIN_1, ADDR_PIN_2, ADDR_PIN_4, ADDR_PIN_8, ADDR_PIN_16};

uint16_t START_POS = 0;
uint16_t STOP_POS = 24;

#define RS485_TRANSMIT  HIGH
#define RS485_RECEIVE   LOW


#define data    11
#define clock   13
#define led     9

Tlc59711 tlc(NUM_TLC);

#define TOTAL_MAGNETS  24
#define TOTAL_BOARDS  5
#define BAUD  1000000
//#define BAUD  115200
uint8_t magnetOutput[TOTAL_MAGNETS] = {};

#define MULTIPLIER    1

const uint16_t packetSize = TOTAL_MAGNETS * TOTAL_BOARDS;
uint16_t byteCount = 0;
uint8_t magCount = 0;
uint16_t packetCount = 0;
uint16_t checksum = 0;
uint8_t indicator = 0;


void setup() {
  //Serial.begin(115200);
  Serial.begin(BAUD);
  pinMode(DATA_DIR_PIN, OUTPUT);
  digitalWrite(DATA_DIR_PIN, RS485_RECEIVE);

  lcd.init();
  lcd.backlight();

  COL = getBoardAddress();

  lcd.print("NEW HUMANS V02");
  lcd.setCursor(0, 1);
  lcd.print("COL: ");
  lcd.print(COL);
  lcd.print("  BAUD:1M");

#ifdef COMMS_TEST
  Serial.println("-------------------------------------------");
  Serial.println("Electromagnetic Control");
  Serial.print("COL: "); Serial.println(COL);
  Serial.println("-------------------------------------------");
#endif

  switch (COL) {
    case 1:
      START_POS = 0;
      STOP_POS = 24;
      break;
    case 2:
      START_POS = 24;
      STOP_POS = 48;
      break;
    case 3:
      START_POS = 48;
      STOP_POS = 72;
      break;
    case 4:
      START_POS =  72;
      STOP_POS = 96;
      break;
    case 5:
      START_POS = 96;
      STOP_POS = 120;
      break;
    default:
      START_POS = 0;
      STOP_POS = 24;
      break;
  }

  initializeArray();
  tlc.beginFast();
  Wire.setClock(400000);

  killPower();

  delay(1000);
  lcd.clear();
  lcd.print("START:");
  lcd.print(START_POS);
  lcd.setCursor(0, 1);
  lcd.print("STOP:");
  lcd.print(STOP_POS);
  delay(1000);
  lcd.clear();
}

void loop() {
#ifdef BOARD_TEST
  boardTestFullPower();
#else
  readIncomingSerial();
#endif
}

void readIncomingSerial() {

  while (Serial.available() > 0) {
    uint8_t inByte = Serial.read();
    if ((byteCount >= START_POS) && (byteCount < STOP_POS)) {
      magnetOutput[magCount] = constrain(inByte, 0, 255);
      magCount++;
    }
    byteCount++;

    if (byteCount >= packetSize) {
      //lcd.print(COUNTED);
      sendDataToMagnets();
      //lcd.clear();
      magCount = 0;
      byteCount = 0;
    }
  }
}

void debugSerialBuffer() {
  Serial.println("MAG: ");
  Serial.println("----------------");
  for (int y = 0; y < 4; y++) {
    for (int x = 0; x < 16; x++) {
      Serial.print(MULTIPLIER * uint16_t(magnetOutput[y * 16 + x]));
      Serial.print(",");
    }
    Serial.println();
    Serial.println();
  }
}

void initializeArray() {
  for (int i = 0; i < TOTAL_MAGNETS; i++) {
    magnetOutput[i] = 0;
  }
}


void boardTest() {
  for (int i = 0; i < TOTAL_MAGNETS; i++) {
    tlc.setChannel(i, 4096);
  }
  tlc.write();
}

void boardTestFullPower() {
  for (int i = 0; i < TOTAL_MAGNETS; i++) {
    tlc.setChannel(i, 65535);
  }
  tlc.write();
}

void boardTestQuarterPower() {
  for (int i = 0; i < TOTAL_MAGNETS; i++) {
    tlc.setChannel(i, 16384);
  }
  tlc.write();
}

void boardTestThreeEighthsPower() {
  for (int i = 0; i < TOTAL_MAGNETS; i++) {
    tlc.setChannel(i, 8192);
  }
  tlc.write();
}

void boardTestHalfPower() {
  for (int i = 0; i < TOTAL_MAGNETS; i++) {
    tlc.setChannel(i, 32769);
  }
  tlc.write();
}

void killPower() {
  for (int i = 0; i < TOTAL_MAGNETS; i++) {
    tlc.setChannel(i, 0);
  }
  tlc.write();
}


void sendDataToMagnets() {
  for (int i = 0; i < TOTAL_MAGNETS; i++) {
    tlc.setChannel(i, magnetOutput[i]);
  }
  tlc.write();
}


uint8_t getBoardAddress() {
  uint8_t currentAddress = 0;
  for (int i = 0; i < TOTAL_BOARDS; i++) {
    pinMode(ADDRESS_PIN[i], INPUT_PULLUP);
    delay(5);
    bool value = digitalRead(ADDRESS_PIN[i]);
    uint8_t addedValue = (1 << i);
    currentAddress += (!value * addedValue);
  }
  return currentAddress;
}

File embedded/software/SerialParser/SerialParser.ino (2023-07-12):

// include the library code:
#include <Wire.h>
#include <LiquidCrystal_I2C.h>

#define VERSION 1.00
#define DATA_DIR_PIN_1  2
#define DATA_DIR_PIN_2  6
#define DATA_DIR_PIN_3  13
#define DATA_DIR_PIN_4  22
#define DATA_DIR_PIN_5  23

#define RS485_TRANSMIT  HIGH
#define RS485_RECEIVE   LOW

#define SERIAL_BAUD     1000000
//#define SERIAL_BAUD     115200
#define SERIAL_BUF_SIZE 120

const uint16_t packetSize = 600;
uint8_t byteBuffer[packetSize];
uint8_t buffer_0[SERIAL_BUF_SIZE];
uint8_t buffer_1[SERIAL_BUF_SIZE];
uint8_t buffer_2[SERIAL_BUF_SIZE];
uint8_t buffer_3[SERIAL_BUF_SIZE];
uint8_t buffer_4[SERIAL_BUF_SIZE];
uint8_t buffer_5[SERIAL_BUF_SIZE];


uint32_t packetCount = 0;
uint32_t byteCount = 0;
uint16_t checksum = 0;

uint8_t checkByte = 0;

bool     firstTimeThrough = true;
uint32_t serialTimer = 0;
uint32_t serialThreshold = 1000; 

LiquidCrystal_I2C lcd(0x27, 16, 2);

void setup() {
  Serial.begin(1000000);
  Serial1.begin(SERIAL_BAUD);
  Serial2.begin(SERIAL_BAUD);
  Serial3.begin(SERIAL_BAUD);
  Serial4.begin(SERIAL_BAUD);
  Serial5.begin(SERIAL_BAUD);

  pinMode(DATA_DIR_PIN_1, OUTPUT);
  digitalWrite(DATA_DIR_PIN_1, RS485_TRANSMIT);
  pinMode(DATA_DIR_PIN_2, OUTPUT);
  digitalWrite(DATA_DIR_PIN_2, RS485_TRANSMIT);
  pinMode(DATA_DIR_PIN_3, OUTPUT);
  digitalWrite(DATA_DIR_PIN_3, RS485_TRANSMIT);
  pinMode(DATA_DIR_PIN_4, OUTPUT);
  digitalWrite(DATA_DIR_PIN_4, RS485_TRANSMIT);
  pinMode(DATA_DIR_PIN_5, OUTPUT);
  digitalWrite(DATA_DIR_PIN_5, RS485_TRANSMIT);

  initializeZeroBuffer();
  
  // set up the LCD's number of columns and rows:
  lcd.init();                      // initialize the lcd 
  lcd.backlight();
  // Print a message to the LCD.
  lcd.print("NEW HUMANS V02");
  lcd.setCursor(0,1);
  lcd.print("V: ");
  lcd.print(VERSION);
  lcd.print("  B: 1M");
  delay(2000);
  lcd.clear();
  lcd.setCursor(0,0);
  //lcd.print("PKT:");
  lcd.print(" LEN:");
  lcd.print(packetSize);

}

void loop() {
  //lcd.setCursor(4,0);
  uint8_t charIndex = 4;
  uint8_t rowIndex = 0;
  byteCount = 0;
  if (Serial.available()) {
    // wait a bit for the entire message to arrive
    delay(24);
    while(Serial.available() > 0){
      serialTimer = millis();
      firstTimeThrough = true;
      
        uint8_t inByte = Serial.read();

      if(byteCount < SERIAL_BUF_SIZE) {
        buffer_1[byteCount] = inByte;
      }

      else if (byteCount < (SERIAL_BUF_SIZE * 2)) {
        buffer_2[byteCount % SERIAL_BUF_SIZE] = inByte;
      }

      else if (byteCount < (SERIAL_BUF_SIZE * 3)) {
        buffer_3[byteCount % SERIAL_BUF_SIZE] = inByte;
      }

      else if (byteCount < (SERIAL_BUF_SIZE * 4)) {
        buffer_4[byteCount % SERIAL_BUF_SIZE] = inByte;
      }

      else {
        buffer_5[byteCount % SERIAL_BUF_SIZE] = inByte;
      }

      ++byteCount;
      
      checksum = (checksum + inByte) % 256;

      //Serial1.write(inByte);
      if(byteCount == packetSize) {
        Serial1.write(buffer_1, SERIAL_BUF_SIZE);
        Serial1.flush(); // block until sent
        
        Serial3.write(buffer_2, SERIAL_BUF_SIZE);
        Serial3.flush(); // block until sent

        Serial2.write(buffer_3, SERIAL_BUF_SIZE);
        Serial2.flush(); // block until sent

        Serial4.write(buffer_4, SERIAL_BUF_SIZE);
        Serial4.flush(); // block until sent

        Serial5.write(buffer_5, SERIAL_BUF_SIZE);
        Serial5.flush(); // block until sent

        lcd.setCursor(charIndex, rowIndex);
        lcd.print(" LEN:");
        lcd.print(byteCount);
        lcd.setCursor(0,1);
        lcd.print("CHK:");
        lcd.print(checkByte);
        lcd.print("  ");
        lcd.setCursor(8,1);
        lcd.print("SUM:");
        lcd.print(checksum);
        lcd.print("  ");
        byteCount = 0;
        checksum = 0;
//        Serial.write('$');

      }

      if(byteCount == (packetSize - 1)){
        checkByte = inByte;
      }
    }
  }

  if(millis() - serialTimer > serialThreshold){
    if(firstTimeThrough){
      firstTimeThrough = false;
      zeroOutMagnets();
    }
  }
}

void initializeZeroBuffer(){
  for(int i=0; i<SERIAL_BUF_SIZE; i++){
    buffer_0[i] = 0;
  }
}

void zeroOutMagnets(){
  Serial1.write(buffer_0, SERIAL_BUF_SIZE);
  Serial1.flush(); // block until sent
        
  Serial3.write(buffer_0, SERIAL_BUF_SIZE);
  Serial3.flush(); // block until sent

  Serial2.write(buffer_0, SERIAL_BUF_SIZE);
  Serial2.flush(); // block until sent

  Serial4.write(buffer_0, SERIAL_BUF_SIZE);
  Serial4.flush(); // block until sent

  Serial5.write(buffer_0, SERIAL_BUF_SIZE);
  Serial5.flush(); // block until sent
}

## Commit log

2019-02-05 Tester Board
    Eagle files for the intial tester board for a small electromagnetic array.
    [ElectromagnetArray_V01.brd, ElectromagnetArray_V01.dxf, ElectromagnetArray_V01.sch]
2019-02-05 Initial Tester Pictures
    Board, mount, and electromagnet pictures
2019-02-06 Updates to Preliminary Design
    Added pull down resistors for the Gate Input on the Transistors.
    All opto isolator LEDs are on the 3V3 rail
    [ElectromagnetArray_V01.brd, ElectromagnetArray_V01.sch]
2019-02-07 Othermill Fix
    Updated layout design for othermill
    [ElectromagnetArray_V01.brd]
2019-03-04 Serial Communication
    Basic Serial Communication between the system and magnetic array
2019-07-20 Serial Communications Test
    Added Teensy Code, Arduino Code, and the current state of the python code.
2019-07-20 Serial PCBs
    Arduino Nano Serial PCB, Teensy Serial PCB, with images of schematic and layout.
    [ArduinoParser.brd, ArduinoParser.sch, MagnetCard.brd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]
2019-08-05 Teensy 3.6 Code
    Code for the Teensy 3.6
2019-08-05 modified nstokes_participle for 1600 value send
    - removed previous WIP version of nstokes
    - added new nstokes_particle folder sent from Jacob
    - modified to compile data and then hand off to thread to send on serial
    - thread only receives new data from draw loop if thread is not busy
    - modified ratio function to fit within 0 to 127
    - found snake / snek function sends negative values so ratio function now zeros those out
    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
2019-08-05 altered teensy code from one large buffer to five smaller ones split among serial
    As in title, maybe a good idea to make it pretty
2019-08-06 new amoeba logic, list reordering, serial bus baud rate changes and writes
    - amoeba directional values changes now, but will still fail eventually
    - ordering of list / bytestring sent to teensy changed to reflect message ordinance
    - serial baud rate and pin changes
    [ordinator.py]
2019-08-12 Added Final Arduino Code for each of the Panels
    Final Arduino Code for each of the panels.
2019-08-12 Runs around 7 frames per second, but seems like the full test
    This version runs at around 7 frames per second, but seems to send the full complement accuratelyg
    Notes that baud rate has been increased to 2000000
2019-08-12 Switch back to 1000000 baud rate for teensy / mac
    switched back to 1000000 on Teensy-Mac comms for now in case there is legacy code out there using 10000000
2019-08-12 Infeed from test branch
    Stalls without delay from five teensies, possibly stalls here as well
2022-03-02 Initial Update V2
    Initial Updated Code, Schematics, and ReadMe for Version 02
    [ElectromagnetController_V3.kicad_pcb, ElectromagnetController_V3.sch, MagnetBank_01.sch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]
2022-03-04 Updated Controller Board Defines
    Changed the Baud Rate, Commented out the BOARD_TEST, and updated the LCD to reflect the changes
2022-03-08 swap parser positions to match board labels
2022-04-05 Updates
    Changed steps (speed of snake), decay rate, framerate from 25 to 30, added var names for mode time intervals
2022-04-18 Zero Out Magnets without Serial
    Zero out the magnets incase we lose connection with computer or USB signal.
2022-04-24 Blooming in place
    - Some errata cleaned up
    - Some formatting changes for readability
    - Added in blooming behavior
    - Added blooming timer to trigger every three works
2023-07-12 pcb, production, and software files for the embedded system
    [ArduinoParser.brd, ArduinoParser.sch, ElectromagnetArray_V01.brd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]
2023-08-03 Added Serial Parser BOM
    [SerialParser_V2.csv, octopart_serialparser_v2.csv]

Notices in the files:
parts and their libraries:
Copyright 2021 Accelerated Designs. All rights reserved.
